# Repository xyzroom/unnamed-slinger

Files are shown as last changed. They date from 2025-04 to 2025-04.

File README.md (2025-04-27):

# unnamed-slinger

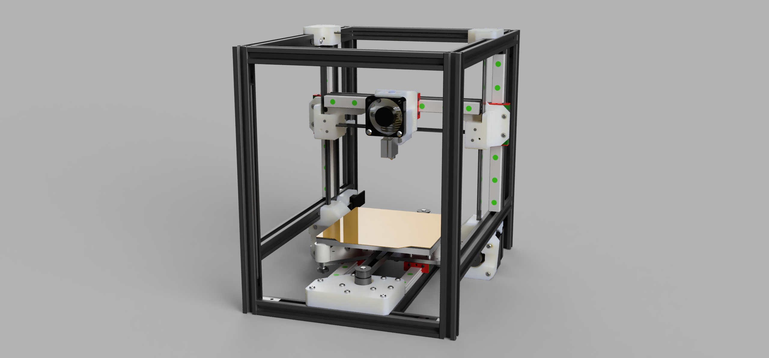
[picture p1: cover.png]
front image


## Overview
- Work-in-progress 3D printer
- CoreXZ bedslinger, to be enclosed in a 22L IKEA SAMLA storage box (38x28x28 cm^3).
- Electronics and filament spool(s) to be housed separately.

## Summary
- 170mm MGN12 rails with MGN12H carriages (2 on Z axis)
- All-bracketed assembly from 1515L extrusions (NOT Makerbeam 1515 extrusions) and slider nuts
- Build footprint of (120mm)^2, Z height not quite at 120mm, can theoretically squeeze there with compromises
- 23.5mm NEMA17 pancake stepper motors (2 on Y axis)
- V6 Volcano in Bowden setup

## Timeline
- V1 (completed): Get basic printer working (V2: modify toolhead and Y axis)
- V2 (ongoing): Add a bunch of fans and chamber temperature sensors. Add air filter

## Rationale, theory, aims
- Lower moving masses
- Components more likely to be flat, square, straight
- Quick to heat up, with potential to reach hotter temperatures if the motors can stay alive
- Separate printer, electronics and filament
- Transparent and removeable enclosure: Typical printers have massive furniture enclosures or their enclosures are built around the printer frame. These can be inconvenient for travel, cleaning and modding.

## Why CoreXZ
I wanted to use up weak pancake steppers I had lying around. CoreXZ is remarkably symmetrical for a box-style frame, and allows A/B steppers to work together for X movements. I was able to squeeze 2 motors into the Y axis.

It is definitely possible to fit something like a tiny AWD CoreXZ, but this would be severely height limited. It would also be harder to modify the toolhead design. With CoreXZ I can offset the entire XZ axis along Y if desired.

## Uncertainties and potential issues:
- Overheating of motors is probably the most signficant problem. In V1-test, I had not yet installed the motor cooling fans, and there was significant skipping on the Y axis, where the motors are below the heated bed. The skipping may also be due to thermal expansion - For some reason I decided to use 2 linear rails on the Y axis, which is a terrible idea for binding, especially under significant temperature changes.
- There is a pitching moment on the X axis due to weight imbalance from the toolhead. (mostly unavoidable, but potentiall avoided by adding a row of fans as counterweight)
- Unsure whether having fans blowing warm air at parts is good or bad. I thought about adding circulation fans to maintain even temperature and protect parts from hot spots, but apparently circulation can cause uneven temperature variations instead.

## Goals and learning
- Use linear rails for the first time
- Use Klipper for the first time
- Use Fusion 360 for the first time
- Finally be able to print with ABS filament
- Improve understanding of CoreXZ/CoreXY motion systems

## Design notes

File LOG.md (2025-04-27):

# Design log

## April 27 2025:
- Uploaded V1-test assembly .step files, EXCLUDING HIWIN configurator models for the the MGN12 rails and MGN12H blocks, due to uncertainty about the copyright

## April 20 2025: V1-test final
- Uploaded all finalised V1-test .step files. Reprinted in PETG and installed within SAMLA box
- Can extend frame in Y direction by about 7mm and X by 1 or 2 mm in the new SAMLA boxes.
- Toolhead is basic (no part cooling)
- Z endstop probing is basic (Makerstop endstop)
- A/B motor cooling designed but not installed
- Y motor cooling not yet designed
- Skipping steps on Y, either due to thermal expansion or motors running too hot
- Y axis redesign for V2: remove 1 linear rail. There are three locations on the Y carriage plate where the remaining MGN12 can be mounted

## April 6 2025:
- Created 'V1-test', beginning to upload 'final' .step files
- Updated Y motor mounts

## April 1 2025
- One week sprint: First version assembled in PLA, excluding motor cooling fans and SAMLA box
- Electronics working without issue, aside from a defective heated bed MOSFET which I replaced
- Layer shifting due to bad belt tensioning on Y axis. Otherwise printer is silent and prints well
- Comments and next changes:
  - Y motor mounts: Change holes to slots so the belt tension can be even higher
  - Wiring and Bowden tube to go to the front of the printer to avoid interference with the Z endstop and XZ belts
  - Sensorless homing (X and Y): Concerning crashes/sensitivities, especially due to temperature variations. Replace with endstops in V2
  - Y carriage: Heating pad thicker than expected and in contact with Y belt holder, causing deformation. Currently spaced by 18mm silicon spacers with extra 1mm printed washer underneath. Also the silicon spacers interfere with the heating pad and are not flush with the bed - does not appear to be an issue. Very minimal increase in binding towards one end of Y axis (bent rail?).
  - XZ motor mounts: Motor wire connectors are so close to the 1515 extrusion that one wire is slightly pinched. Not urgent
  - Volcano clone: Thermistor and heater cartridge wires must be bent a concerning amount

## March 14 2025
- Increased spacing around Y motors by 1mm for airflow
- Edited Y motor mounts and Y carriage belt holder to be more sensible CAD-wise

## March 13 2025
- Started repo, upload images and files later
- Parts on their way
- Designing part cooling for V2
- Figuring out Bowden extruder placement

- Assessing motor cooling options for Y axis steppers
- Assessing air circulation options under heated bed
- Considering static part cooling fans on X axis behind toolhead

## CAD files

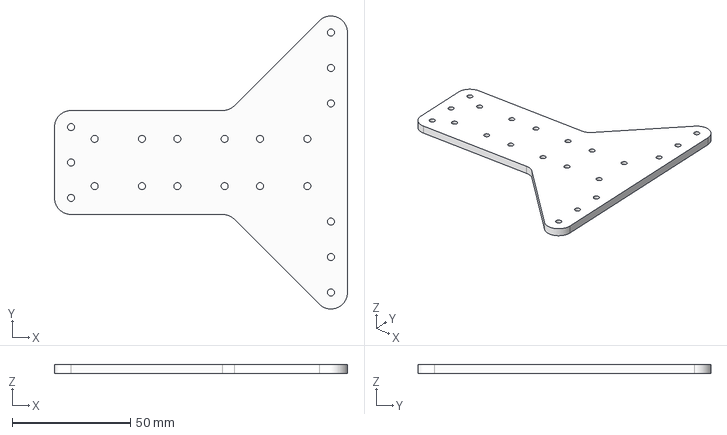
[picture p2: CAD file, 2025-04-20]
V1-test/Step files/Aluminium plate, cut/Y Carriage Plate v25.step
124.0 x 124.0 x 4.00 mm

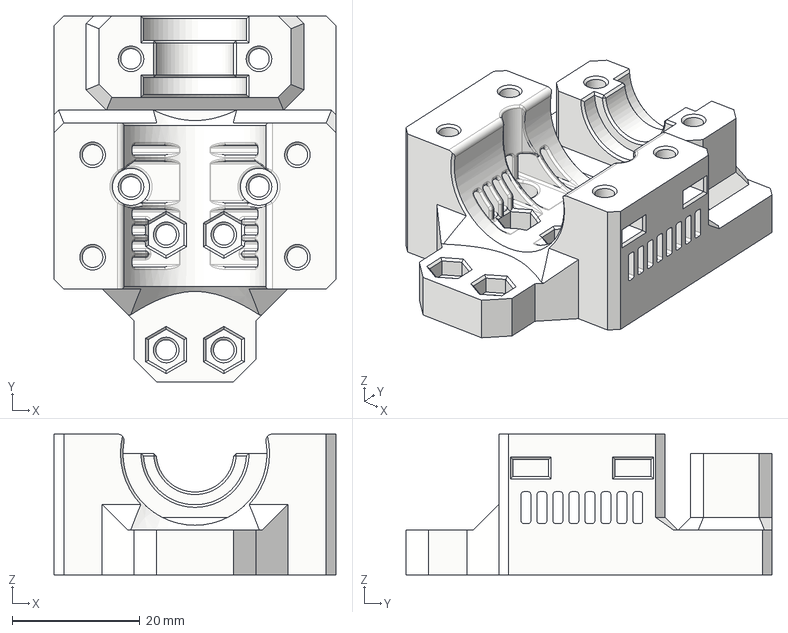
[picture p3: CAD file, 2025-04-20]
V1-test/Step files/Printed parts/Toolhead BASIC/XCarriage v37.step
44.0 x 57.2 x 22.0 mm

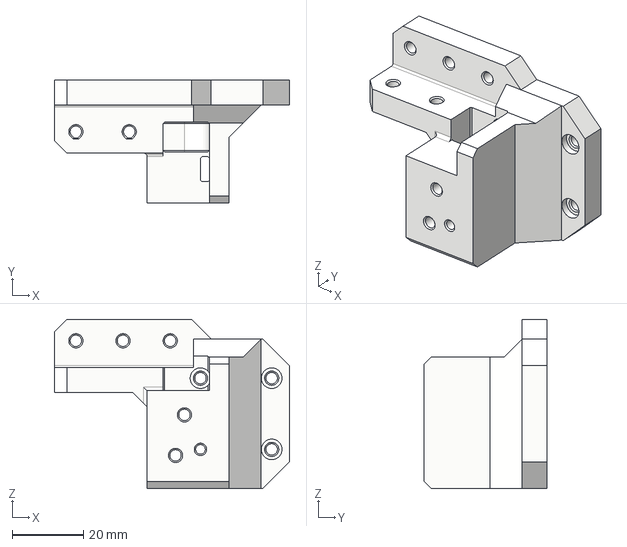
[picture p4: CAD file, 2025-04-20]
V1-test/Step files/Printed parts/X axis/RightXZCarriage v21.step
66.0 x 34.5 x 47.5 mm

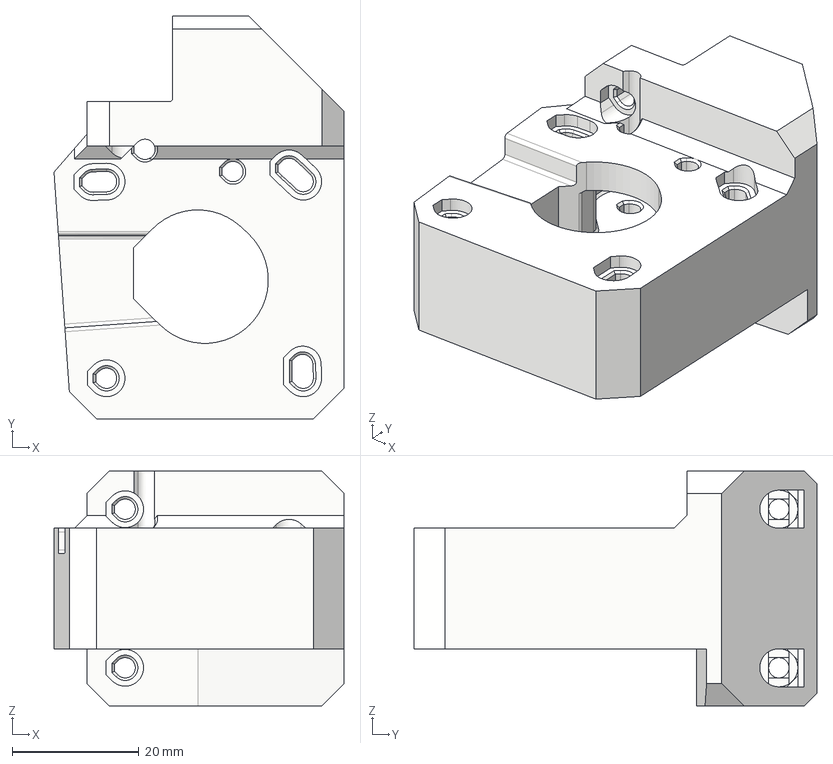
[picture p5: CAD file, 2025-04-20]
V1-test/Step files/Printed parts/XZ (mirror)/XZMotorMount v33.step
45.7 x 63.5 x 37.0 mm

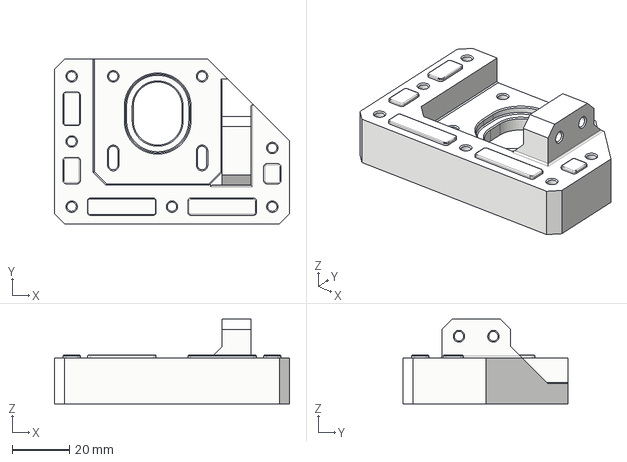
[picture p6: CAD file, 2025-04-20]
V1-test/Step files/Printed parts/Y axis (mirror)/Y Motor Mount v28.step
82.0 x 57.5 x 29.5 mm

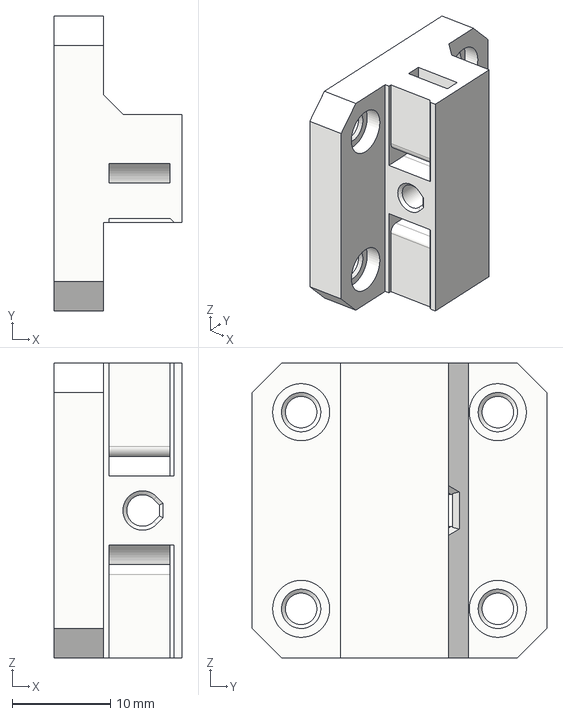
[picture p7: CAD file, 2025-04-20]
V1-test/Step files/Printed parts/Y carriage/YCarriageBeltHolder v20.step
13.0 x 30.0 x 30.0 mm

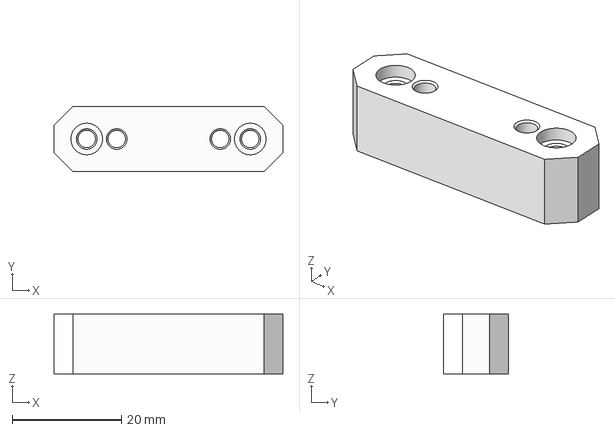
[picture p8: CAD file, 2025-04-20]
V1-test/Step files/Printed parts/Z endstop probing BASIC/ZEndstopMount v11.step
42.0 x 12.0 x 11.0 mm

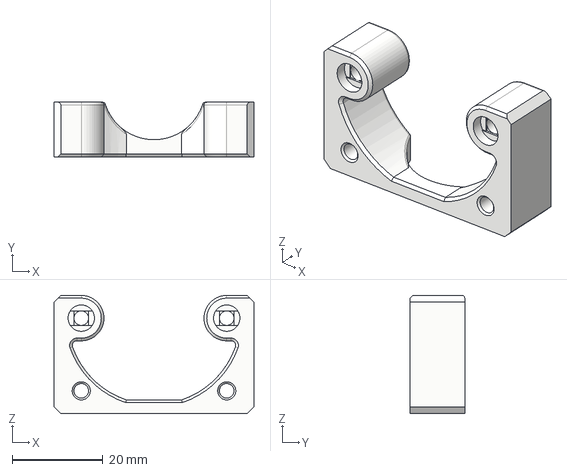
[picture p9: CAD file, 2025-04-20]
V1-test/Step files/Printed parts/Toolhead BASIC/PartCoolingFanMount v17.step
44.0 x 12.0 x 26.0 mm

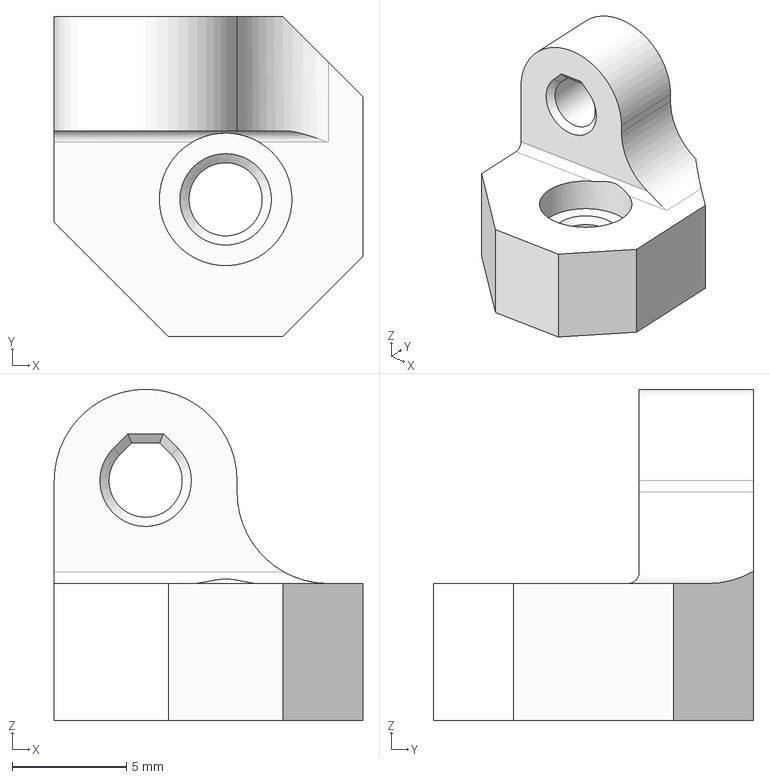
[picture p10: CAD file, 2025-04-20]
V1-test/Step files/Printed parts/XZ (mirror)/XZMotorFanMount v10.step
13.5 x 14.0 x 14.5 mm

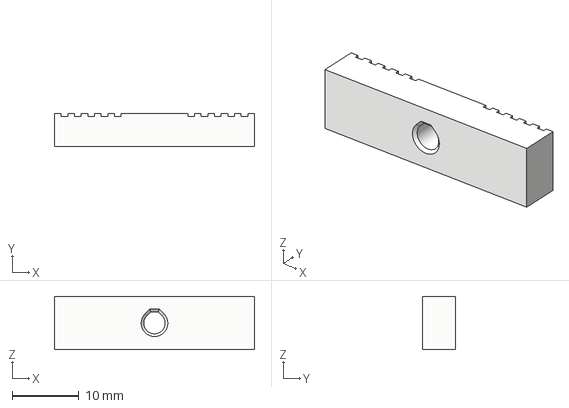
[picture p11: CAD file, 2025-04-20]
V1-test/Step files/Printed parts/Y carriage/YCarriageBeltClamp v10.step
30.0 x 5.00 x 7.95 mm

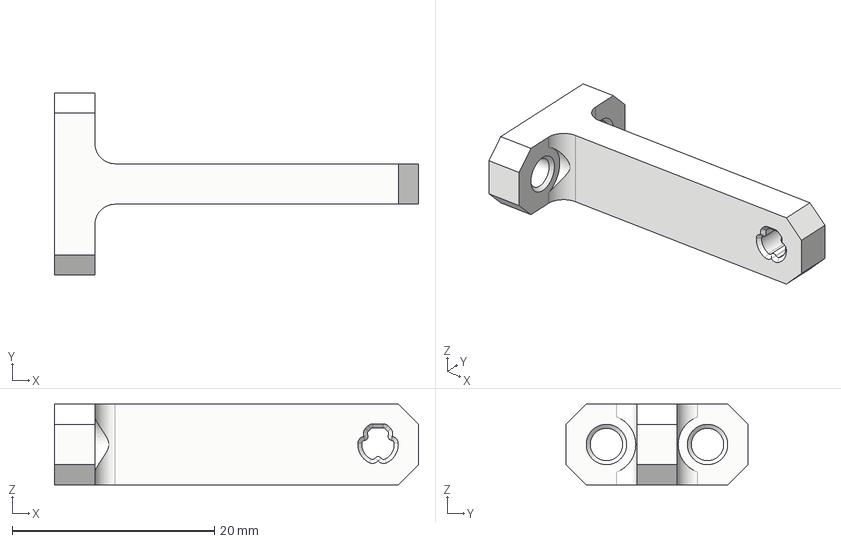
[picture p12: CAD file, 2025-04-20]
V1-test/Step files/Printed parts/Z endstop probing BASIC/ZEndstopProbeMount v16.step
36.0 x 18.0 x 8.00 mm

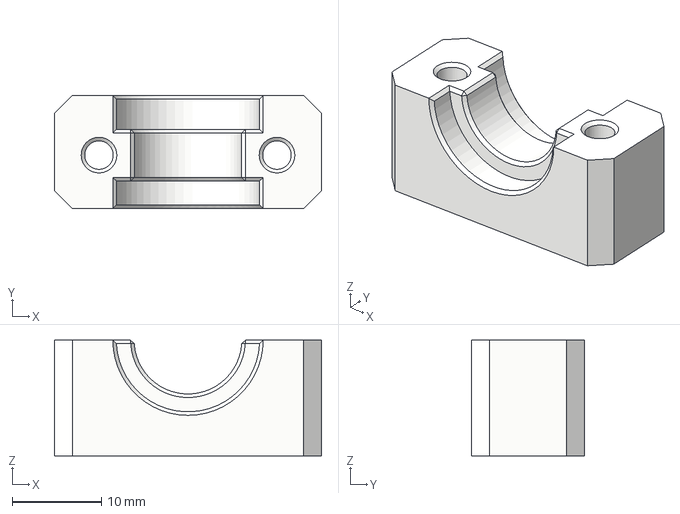
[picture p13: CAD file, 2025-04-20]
V1-test/Step files/Printed parts/Toolhead BASIC/HotEndClamp v12.step
30.0 x 12.7 x 13.0 mm

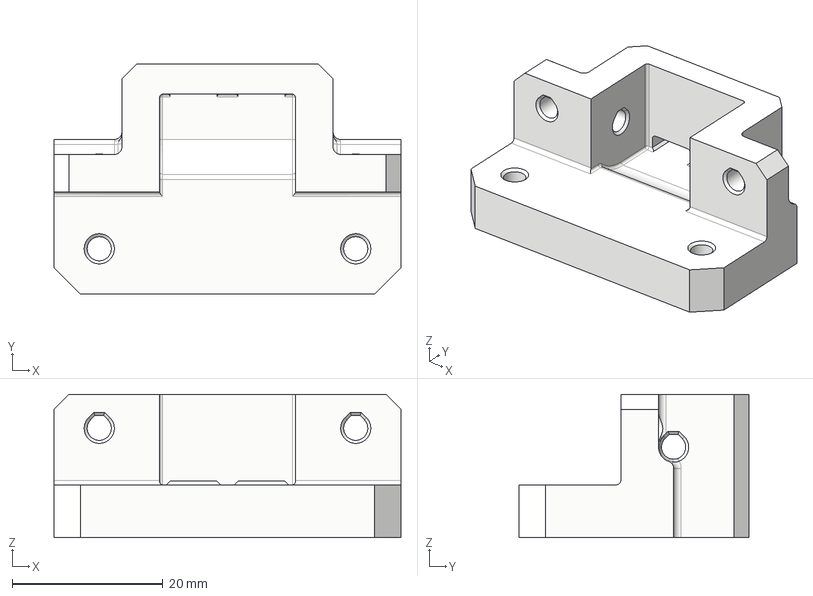
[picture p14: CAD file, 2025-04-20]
V1-test/Step files/Printed parts/XZ (mirror)/XZIdlerMount v15.step
46.0 x 30.5 x 19.0 mm

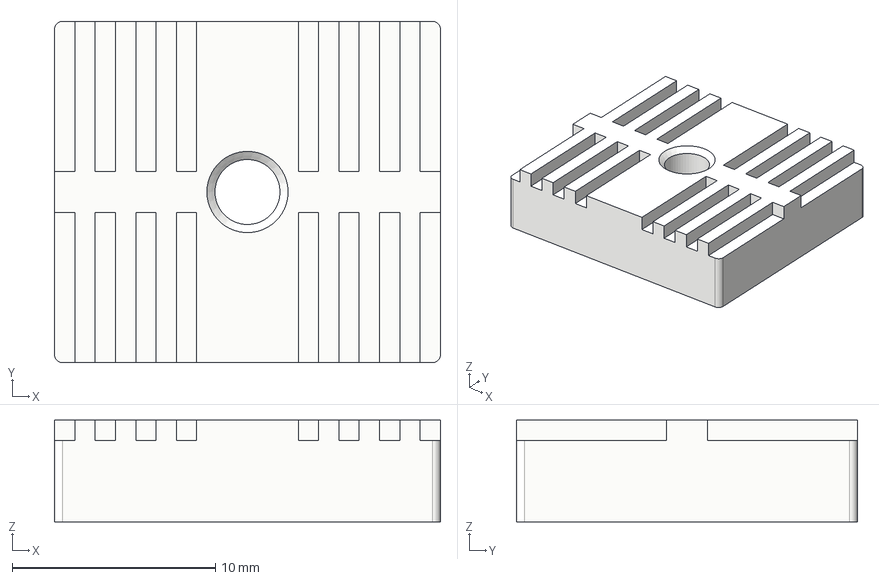
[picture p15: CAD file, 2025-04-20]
V1-test/Step files/Printed parts/Toolhead BASIC/XCarriageBeltClamp v10.step
19.0 x 16.8 x 5.00 mm

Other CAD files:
V1-test/Step files/Printed parts/X axis/LeftXZCarriage v33.step
V1-test/Step files/Printed parts/Toolhead BASIC/XCarriageBeltHolder v17.step

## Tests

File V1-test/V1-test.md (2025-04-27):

# V1-test summary

front image
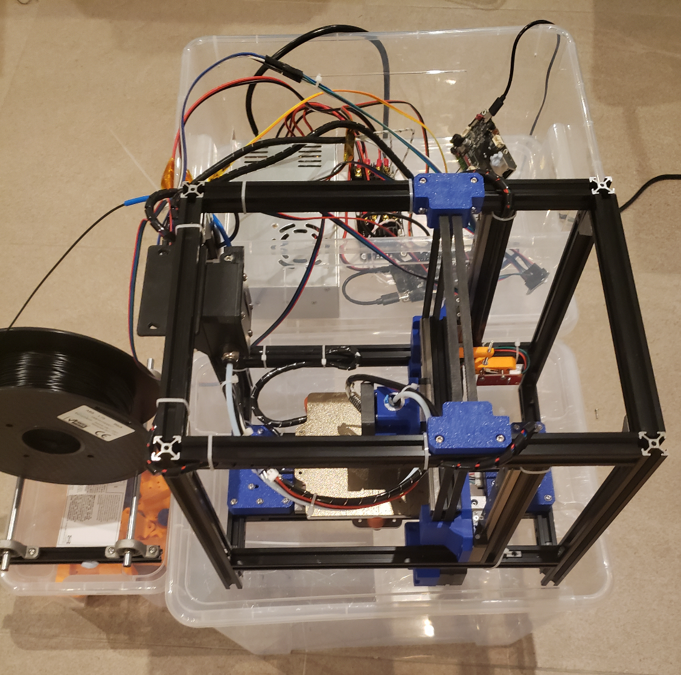
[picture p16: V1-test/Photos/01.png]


## Y carriage plate
I had this laser cut from 4mm thick 1060 aluminium

## Printed parts
- .step files have been provided
- Supports are unnecessary, but parts are not necessarily in the correct print orientation
- Print in 0.1mm or 0.2mm layer height
- Inner/outer perimeter order. Do not do outer/inner if seams affect the accuracy of small holes
- There are no circular overhangs but bridging capability is necessary. Consider turning off 'thick bridges'

## Fixtures
- M3 screws, most of which are 2mm button heads
- Some brackets need M4

## CAD information
- In the assembly file, MGN12 rails and MGN12H blocks have been removed
- Fixtures may not be modelled accurately, to the correct lengths. Also add and remove spacers/washers where needed

## First iteration summary:
- Basic toolhead (no part cooling)
- Motor cooling not installed

## Issues:
- Skipping steps on Y. Either binding due to thermal expansion with the 2 linear rails, or motors running too hot
- Inconsistent sensorless homing on X/Y due to significant temperature range

## Changes for V2:
- Add endstops on X and Y axes
- Design Y axis motor cooling
- Redesign Y axis to use only 1 linear rail. (There are three locations on the Y carriage plate to mount the MGN12)
- Design part cooling on the toolhead
- Design row of part cooling fans behind the X axis
- Design air circulation fans and carbon filter
